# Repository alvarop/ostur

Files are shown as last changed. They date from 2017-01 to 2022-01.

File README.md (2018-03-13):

# Ostur - Cheese cave controller!

This is a work in progress for a cheese cave controller system.
The goal is to be able to control a mini fridge to get the right conditions for cheesemaking.

The project consists of:

* [Hardware](hw/) - A microcontroller and various temperature/humidity sensors
* [Firmware](fw/2.0/) - Code in the microcontroller to control the fridge and measure temperature/humidity values
* [Software](sw/2.0/) - Python scripts to communicate with the microcontroller to log and plot data

So far, it's been used to [make Brie](https://imgur.com/a/cGHID) [successfully](https://imgur.com/B5qB1kU)!

Once it's more user friendly, I'll add usage instructions so others can reproduce the setup.

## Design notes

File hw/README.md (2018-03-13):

# Ostur Hardware

To make some brie, there are 3 main components required:
1. An [Ostur controller](controller/) PCB
2. A controllable power outlet relay module. I'm using [this one](https://www.adafruit.com/product/2935) from Adafruit
3. 2+ [Ostur temperature/humidity sensors](humidity/). One for the fridge temperature and the rest for each aging container (if any).

Optional components are:
1. [Silicon Labs BLED112](https://www.digikey.com/products/en?keywords=1446-1030-ND) USB dongle for receiving BLE beacon data of the temperature/humidity.

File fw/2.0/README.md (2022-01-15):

# Ostur Firmware

The latest Ostur hardware uses the NRF52 microcontroller and the [Apache Mynewt](https://mynewt.apache.org/) OS for the firmware.

## Building the Firmware

1. Install the newt tool. [Instructions here](https://mynewt.apache.org/os/get_started/get_started/).
2. Install the [GNU Arm Embedded Toolchain](https://developer.arm.com/open-source/gnu-toolchain/gnu-rm/downloads)
3. Clone this repo `git clone https://github.com/alvarop/ostur.git`
4. Cd into the fw directory (this one) `cd fw/2.0/`
5. Run `newt install` to get the Mynewt libraries
6. Run `newt build ostur_sensor_boot` to build the bootloader
7. Run `newt build ostur_sensor`

## Loading the Firmware (using an [NRF52DK](https://www.nordicsemi.com/eng/Products/Bluetooth-low-energy/nRF52-DK) as a programmer)
1. Make sure the [JLink tools](https://www.segger.com/downloads/jlink/) are installed
2. Connect the **Debug Out** connector on the NRF52DK (or on any JLink programmer) to the Ostur's SWD connector (on the bottom)
3. Run `newt load ostur_sensor_boot` to load the bootloader
4. Run `newt run ostur_sensor 0` to load the main firmware and enter a gdb debugging session. Press `c + enter` to start running the code.

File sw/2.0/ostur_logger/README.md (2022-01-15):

# Ostur Logger Setup

## On Raspberry Pi

1. Clone repo to raspberry pi (or scp it over)
2. Run `./support/install_dependencies.sh` to get required software
3. Run `./support/setup.sh` to configure everything and start the server

If you just changed a few files and don't want to go through the whole pipenv process again, you can use `./support/update.sh`. This will just restart the services.

### Monitoring
To monitor packets arriving run:

`sudo tail -f /var/log/supervisor/ostur-logger-app-stdout---supervisor-KsDl4b.log`

Note that the last few characters, `KsDl4b` in this case, change everytime supervisor restarts. It's easy to just tab complete with whatever is there.

To check for errors, just replace stdout for stderr in the command.

## Local Development
`pip install -r requirements.txt`
Run `pipenv run python ostur_logger.py --port /dev/ttyUSB0 --baud_rate 115200 --db sqlite_db_filename.db`

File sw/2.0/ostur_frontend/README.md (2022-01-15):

# Ostur Frontend Setiup

## On Raspberry Pi

1. Clone repo to raspberry pi (or scp it over)
2. Run `./support/install_dependencies.sh` to get required software
3. Run `./support/setup.sh` to configure everything and start the server

**NOTE:** Python files copied over to /var/flaskapp/ostur_frontend, so if you edit the ones here, it won't change.

If you just changed a few files and don't want to go through the whole pipenv process again, you can use `./support/update.sh`. This will just rsync the changed files over and restart the services.

## Local Development

### Gunicorn
`pip install -r requirements.txt`
Run `export DATABASE=/path/to/ostur.db; pipenv run gunicorn --reload src:app`

### Flask Profiler

Temporarily install `pipenv install werkzeug`

Run `export DATABASE=/path/to/ostur.db; pipenv run python ./src/profile-flask.py`

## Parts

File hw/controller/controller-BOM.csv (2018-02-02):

Title | Ostur Controller
Revision | 2.0
Date | 2018-01-22
Generated | Fri 02 Feb 2018 03:28:43 AM PST
Company | alvarop.com
Comment 1
Comment 2
Comment 3
Comment 4
Total Parts | 49
Total Unique Parts | 29
Ref | Qty | Value | Footprint | MPN
AE1 | 1 | Antenna | alvarop:AMCA31-2R450G-S1F-T3
C10 C11 C5 | 3 | 1uF | Capacitors_SMD:C_0603 | CL21F105ZAFNNNG
C2 | 1 | 10nF | Capacitors_SMD:C_0603 | CL21B103KBANNNC
C17 C4 C6 C1 | 4 | 100nF | Capacitors_SMD:C_0603 | CL21B104MBCNNNC
C9 C3 | 2 | 4.7uF | Capacitors_SMD:C_0603 | CL21A475KQFNNNG
C12 C7 | 2 | 12pF | Capacitors_SMD:C_0603
C8 | 1 | 100pF | Capacitors_SMD:C_0603
C13 | 1 | 0.8pF | Capacitors_SMD:C_0603
C14 C15 | 2 | DNP | Capacitors_SMD:C_0603
D3 | 1 | LED2 | LEDs:LED_0603 | LG R971-KN-1
D2 | 1 | LED1 | LEDs:LED_0603 | LG R971-KN-1
D1 | 1 | LED0 | LEDs:LED_0603 | LG R971-KN-1
J2 | 1 | USB_OTG | footprints:USB_MICRO_B | 10118192-0001LF
J3 | 1 | UART | Pin_Headers:Pin_Header_Straight_1x03_Pitch1.27mm
J1 | 1 | ARM-SWD | alvarop:ARM_SWD_SMD
L1 | 1 | 3.9nH | Resistors_SMD:R_0603
P14 | 1 | I2C0 | Pin_Headers:Pin_Header_Straight_1x04_Pitch2.54mm
P15 | 1 | I2C1 | Pin_Headers:Pin_Header_Straight_1x04_Pitch2.54mm
P16 | 1 | I2C2 | Pin_Headers:Pin_Header_Straight_1x04_Pitch2.54mm
P17 | 1 | I2C3 | Pin_Headers:Pin_Header_Straight_1x04_Pitch2.54mm
P2 | 1 | FRIDGE | Pin_Headers:Pin_Header_Straight_1x02_Pitch2.54mm
R5 R4 R3 | 3 | 680 | Resistors_SMD:R_0603 | RC0805JR-07680RL
R11 R12 R9 R10 R13 R14 R21 R22 R23 R24 R26 | 11 | 10k | Resistors_SMD:R_0603 | 311-10KARCT-ND
R1 | 1 | 0 | Resistors_SMD:R_0603
U3 | 1 | tca9546a | Housings_SSOP:TSSOP-16_4.4x5mm_Pitch0.65mm | TCA9546APWR
U2 | 1 | MIC550X | footprints:SOT-23(M5)
U8 | 1 | SHT3x-DIS | footprints:SHT3x
U1 | 1 | NRF52810-QCAA | alvarop:NRF52810_QCAA_QFN32
Y1 | 1 | 32MHz | Crystals:Crystal_SMD_2016-4pin_2.0x1.6mm | CX2016DB32000D0FLJCC
BOM made with KICAD_BOM_WIZARD (https://github.com/HashDefineElectronics/KiCad_BOM_Wizard.git)
Generated Fri 02 Feb 2018 03:28:43 AM PST

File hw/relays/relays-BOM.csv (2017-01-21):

Title
Revision
Date
Generated | Fri 20 Jan 2017 06:25:38 PM PST
Company
Comment 1
Comment 2
Comment 3
Comment 4
Total Parts | 8
Total Unique Parts | 6
Ref | Qty | Value | Footprint | MPN
D1 | 1 | D | footprints:SOD-80 | LL4148
K1 | 1 | EE2-3NU | footprints:EE2-3NU | EE2-3NU-L
P1 | 1 | CONN_01X03 | Pin_Headers:Pin_Header_Straight_1x03
P2 P3 P4 | 3 | CONN_01X02 | Pin_Headers:Pin_Header_Straight_1x02
Q1 | 1 | MMBT3904 | TO_SOT_Packages_SMD:SOT-23 | MMBT3904 215
R1 | 1 | 1k1 | Resistors_SMD:R_0805 | RMCF0805JT1K00
BOM made with KICAD_BOM_WIZARD (https://github.com/HashDefineElectronics/KiCad_BOM_Wizard.git)
Generated Fri 20 Jan 2017 06:25:38 PM PST

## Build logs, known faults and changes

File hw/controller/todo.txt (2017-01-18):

Add jumper for 5V/3V from UART1 connector
Add silkscreen to mark uart3/spi ground and power

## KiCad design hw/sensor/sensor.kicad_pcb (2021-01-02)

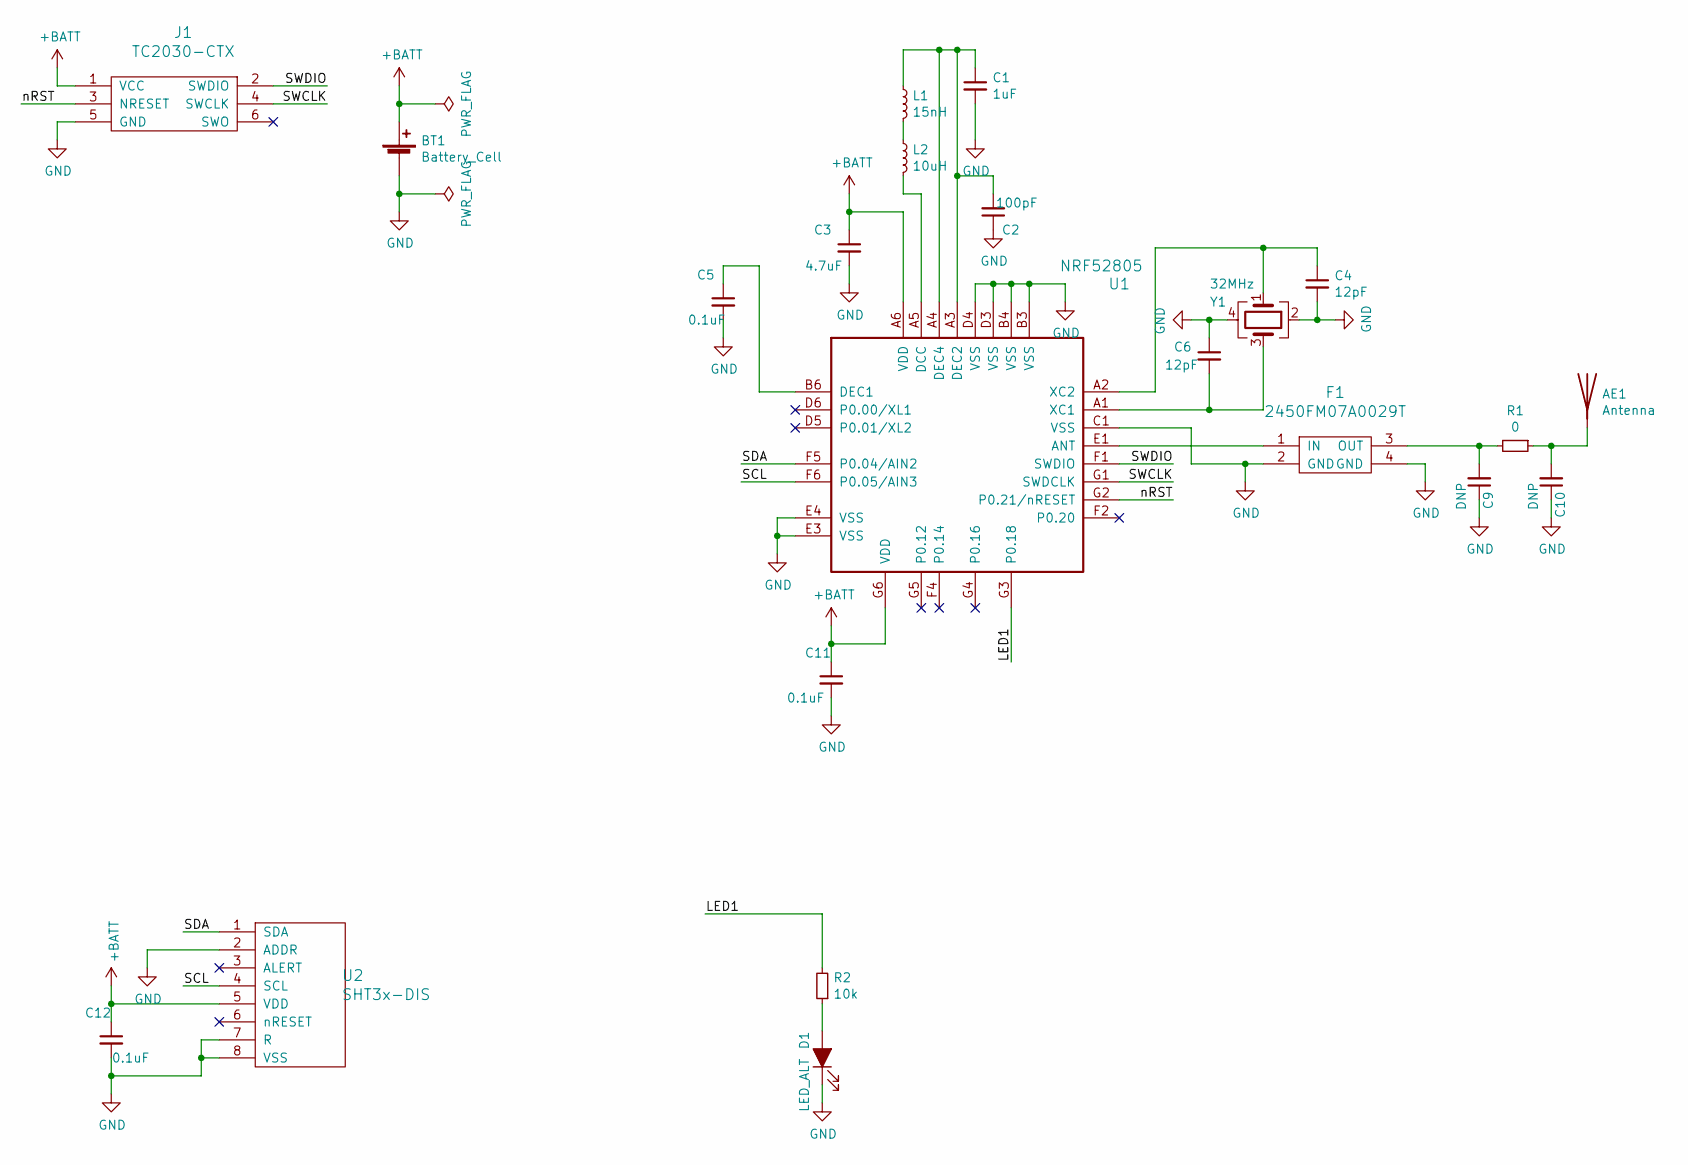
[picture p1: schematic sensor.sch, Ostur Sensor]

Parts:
AE1: Antenna; AMCA31-2R450G-S1F-T3; MPN AMCA31-2R450G-S1F-T3
BT1: Battery_Cell; BAT-HLD-001-THM; MPN BATT-HLD-001-THM
C1: 1uF; C_0402_1005Metric; MPN CC0402KRX5R5BB105
C2: 100pF; C_0402_1005Metric; MPN UMK105CG101JV-F
C3: 4.7uF; C_0402_1005Metric; MPN GRM155R60J475ME47D
C4, C6: 12pF; C_0402_1005Metric; MPN C0402C120J5GACTU
C5, C11, C12: 0.1uF; C_0402_1005Metric; MPN GRM155R61A104KA01D
C9, C10: DNP; C_0402_1005Metric
D1: LED_ALT; LED_0402_1005Metric; MPN QBLP595-IG
F1: 2450FM07A0029T; MPN 2450FM07A0029T
J1: TC2030-CTX; TC2030-NL
L1: 15nH; L_0402_1005Metric; MPN HK100515NJ-T‎
L2: 10uH; L_0603_1608Metric; MPN ‎LQM18FN100M00D‎
R1: 0; R_0402_1005Metric; MPN RC1005J000CS
R2: 10k; R_0402_1005Metric; MPN RC0402JR-0710KL
U1: NRF52805; MPN NRF52805-CAAA-R
U2: SHT3x-DIS; SHT3x; MPN SHT30-DIS-P2.5KS
Y1: 32MHz; Crystal_SMD_2016-4Pin_2.0x1.6mm; MPN CX2016DB32000D0FLJCC

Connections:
+BATT: BT1.1 (+), C3.1, C11.1, C12.1, J1.1 (VCC), U1.A6 (VDD), U1.G6 (VDD), U2.5 (VDD)
/LED1: R2.2, U1.G3 (P0.18)
/SCL: U1.F6 (P0.05/AIN3), U2.4 (SCL)
/SDA: U1.F5 (P0.04/AIN2), U2.1 (SDA)
/SWCLK: J1.4 (SWCLK), U1.G1 (SWDCLK)
/SWDIO: J1.2 (SWDIO), U1.F1 (SWDIO)
/nRST: J1.3 (NRESET), U1.G2 (P0.21/nRESET)
GND: BT1.2 (-), C1.2, C2.1, C3.2, C4.2, C5.2, C6.1, C9.1, C10.1, C11.2, C12.2, D1.1 (K), F1.2 (GND), F1.4 (GND), J1.5 (GND), U1.B3 (VSS), U1.B4 (VSS), U1.C1 (VSS), U1.D3 (VSS), U1.D4 (VSS), U1.E3 (VSS), U1.E4 (VSS), U2.2 (ADDR), U2.7 (R), U2.8 (VSS), Y1.2, Y1.4
unnamed: AE1.1, C10.2, R1.1
unnamed: C1.1, C2.2, L1.1, U1.A3 (DEC2), U1.A4 (DEC4)
unnamed: C4.1, U1.A2 (XC2), Y1.1
unnamed: C5.1, U1.B6 (DEC1)
unnamed: C6.2, U1.A1 (XC1), Y1.3
unnamed: C9.2, F1.3 (OUT), R1.2
unnamed: D1.2 (A), R2.1
unnamed: F1.1 (IN), U1.E1 (ANT)
unnamed: L1.2, L2.1
unnamed: L2.2, U1.A5 (DCC)

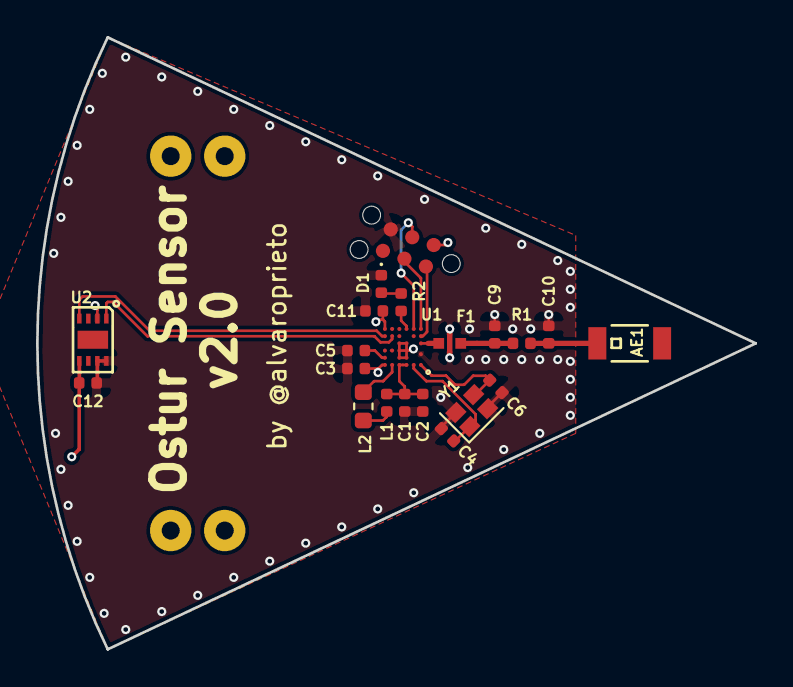
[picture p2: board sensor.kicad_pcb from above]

Board: 4 copper layers, 39.9 x 34.0 mm, 22 parts (1 on the bottom side), 18 nets.

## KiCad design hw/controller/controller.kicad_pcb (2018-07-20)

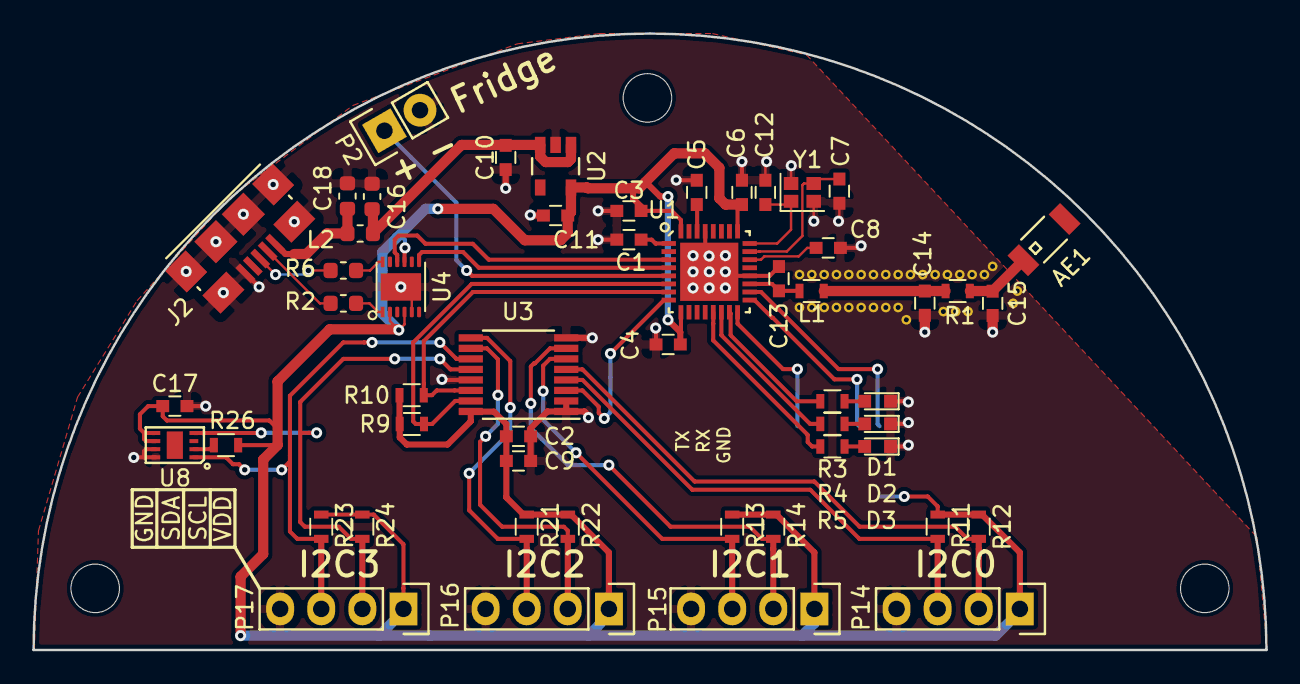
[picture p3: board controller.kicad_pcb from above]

Board: 2 copper layers, 76.2 x 38.1 mm, 54 parts (1 on the bottom side), 40 nets.

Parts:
AE1: Antenna; AMCA31-2R450G-S1F-T3
C1, C4, C6, C17: 100nF; C_0603
C2: 10nF; C_0603
C3, C9: 4.7uF; C_0603
C5, C10, C11: 1uF; C_0603
C7, C12: 12pF; C_0603
C8: 100pF; C_0603
C13: 0.8pF; C_0603
C14, C15: DNP; C_0603
C16: 100nF; C_0603_1608Metric
C18: 10nF; C_0603_1608Metric
D1: LED0; LED_0603
D2: LED1; LED_0603
D3: LED2; LED_0603
J1: ARM-SWD; ARM_SWD_SMD
J2: USB_OTG; USB_MICRO_B
L1: 3.9nH; R_0603
L2: FB; R_0603_1608Metric
P2: FRIDGE; Pin_Header_Straight_1x02
P14: I2C0; Pin_Header_Straight_1x04
P15: I2C1; Pin_Header_Straight_1x04
P16: I2C2; Pin_Header_Straight_1x04
P17: I2C3; Pin_Header_Straight_1x04
R1: 0; R_0603
R2, R6: 27; R_0603_1608Metric
R3, R4, R5: 680; R_0603
R9, R10, R11, R12, R13, R14, R21, R22, R23, R24, R26: 10k; R_0603
U1: NRF52810-QCAA; NRF52810_QCAA_QFN32
U2: MIC550X; SOT-23(M5)
U3: tca9546a; TSSOP-16_4.4x5mm_Pitch0.65mm
U4: FT234XD; FTDI_DFN12
U8: SHT3x-DIS; SHT3x
Y1: 32MHz; Crystal_SMD_2016-4pin_2.0x1.6mm

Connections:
+5V: C10.1, C16.1, L2.2, U2.1, U2.3
/ADDR_LOCAL: R26.1, U8.2
/FRIDGE: P2.1, U1.5
/LED0: R3.2, U1.15
/LED1: R4.2, U1.14
/LED2: R5.2, U1.13
/SCL: R10.2, U1.7, U3.14
/SCL0: P14.2, R12.2, U3.5
/SCL1: P15.2, R14.2, U3.7
/SCL2: P16.2, R22.2, U3.10
/SCL3: P17.2, R24.2, U3.12, U8.4
/SDA: R9.2, U1.6, U3.15
/SDA0: P14.3, R11.2, U3.4
/SDA1: P15.3, R13.2, U3.6
/SDA2: P16.3, R21.2, U3.9
/SDA3: P17.3, R23.2, U3.11, U8.1
/SWDCLK: J1.4, U1.17
/SWDIO: J1.2, U1.18
/TCA_nRST: U1.8, U3.3
/UART1_RX: U1.4, U4.7
/UART1_TX: U1.3, U4.10
/USB_DM: J2.2, R2.1
/USB_DP: J2.3, R6.2
/VDD_5: C18.1, J2.1, L2.1
/nRST: J1.10, U1.16
GND: C1.2, C2.2, C3.2, C4.2, C5.2, C6.2, C7.2, C8.1, C9.2, C10.2, C11.2, C12.1, C13.1, C14.1, C15.1, C16.2, C17.2, C18.2, D1.1, D2.1, D3.1, J1.3, J1.5, J2.5, J2.6, P2.2, P14.4, P15.4, P16.4, P17.4, U1.20, U1.29, U2.2, U3.1, U3.2, U3.8, U3.13, U4.5, U8.7, U8.8, Y1.2, Y1.4
unnamed: AE1.1, C15.2, R1.2
unnamed: C1.1, U1.1
unnamed: C5.1, U1.30
unnamed: C7.1, U1.23, Y1.3
unnamed: C8.2, U1.22
unnamed: C12.2, U1.24, Y1.1
unnamed: C13.2, L1.1, U1.19
unnamed: C14.2, L1.2, R1.1
unnamed: D1.2, R3.1
unnamed: D2.2, R4.1
unnamed: D3.2, R5.1
unnamed: R2.2, U4.1
unnamed: R6.1, U4.12
VDD: C2.1, C3.1, C4.1, C6.1, C9.1, C11.1, C17.1, J1.1, P14.1, P15.1, P16.1, P17.1, R9.1, R10.1, R11.1, R12.1, R13.1, R14.1, R21.1, R22.1, R23.1, R24.1, R26.2, U1.9, U1.25, U1.32, U2.5, U3.16, U4.2, U4.4, U4.9, U8.5, U8.6

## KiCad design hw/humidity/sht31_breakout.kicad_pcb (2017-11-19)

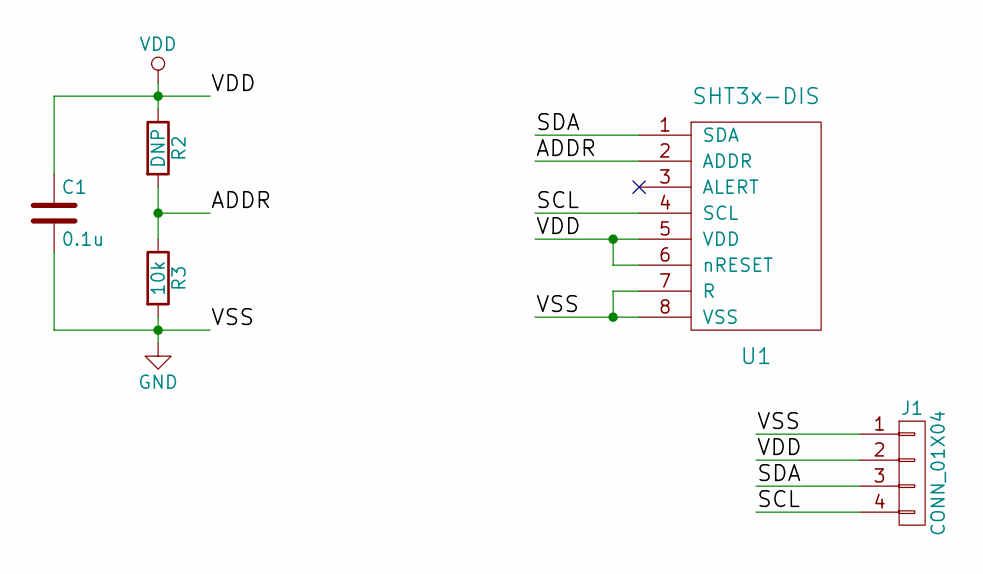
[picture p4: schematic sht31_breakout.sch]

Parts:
C1: 0.1u; C_0603
J1: CONN_01X04; Pin_Header_Straight_1x04_Pitch2.54mm
R2: DNP; C_0603
R3: 10k; C_0603
U1: SHT3x-DIS; SHT3x

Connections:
/ADDR: R2.2, R3.1, U1.2 (ADDR)
/SCL: J1.4, U1.4 (SCL)
/SDA: J1.3, U1.1 (SDA)
GND: C1.2, J1.1, R3.2, U1.7 (R), U1.8 (VSS)
VDD: C1.1, J1.2, R2.1, U1.5 (VDD), U1.6 (nRESET)

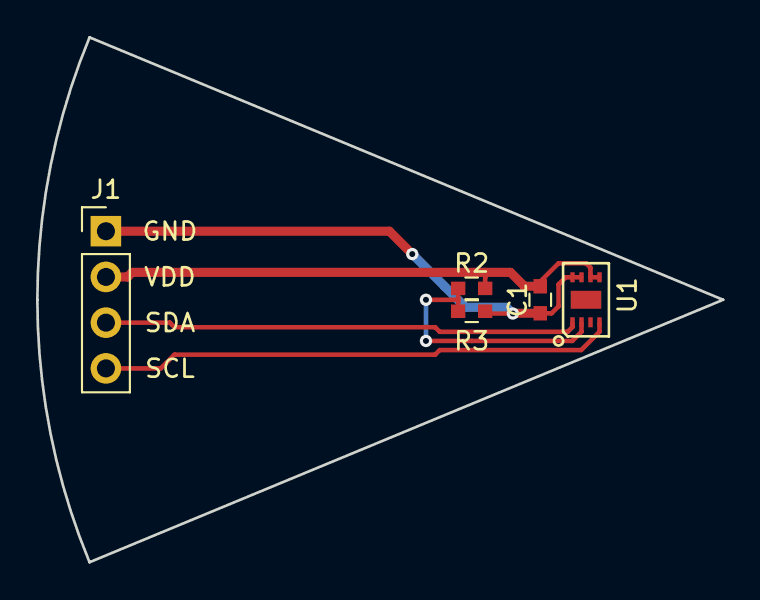
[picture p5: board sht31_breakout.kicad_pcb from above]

Board: 2 copper layers, 38.1 x 29.2 mm, 5 parts (0 on the bottom side), 5 nets.

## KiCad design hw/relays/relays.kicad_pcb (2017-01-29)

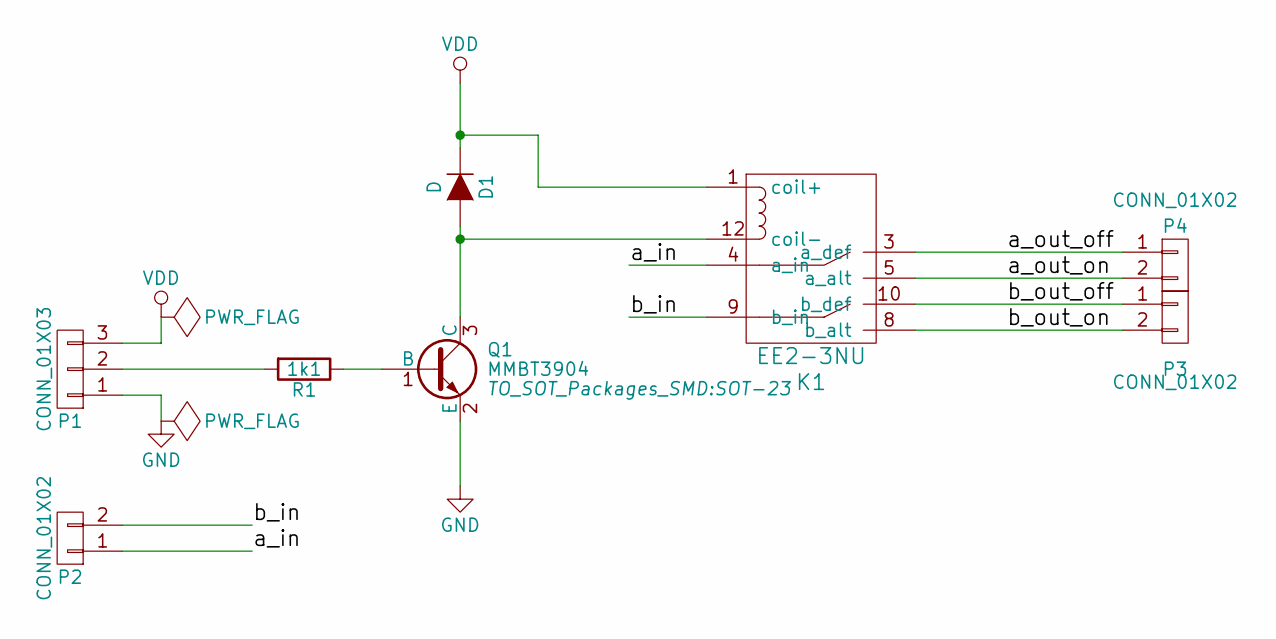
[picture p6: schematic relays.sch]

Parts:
D1: D; SOD-80; MPN LL4148
K1: EE2-3NU; MPN EE2-3NU-L
P1: CONN_01X03; Pin_Header_Straight_1x03
P2, P3, P4: CONN_01X02; Pin_Header_Straight_1x02
Q1: MMBT3904; SOT-23; MPN MMBT3904,215
R1: 1k1; R_0805; MPN RMCF0805JT1K00

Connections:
/a_in: K1.4 (a_in), P2.1
/a_out_off: K1.3 (a_def), P4.1
/a_out_on: K1.5 (a_alt), P4.2
/b_in: K1.9 (b_in), P2.2
/b_out_off: K1.10 (b_def), P3.1
/b_out_on: K1.8 (b_alt), P3.2
GND: P1.1, Q1.2 (E)
unnamed: D1.2 (A), K1.12 (coil-), Q1.3 (C)
unnamed: P1.2, R1.2
unnamed: Q1.1 (B), R1.1
VDD: D1.1 (K), K1.1 (coil+), P1.3

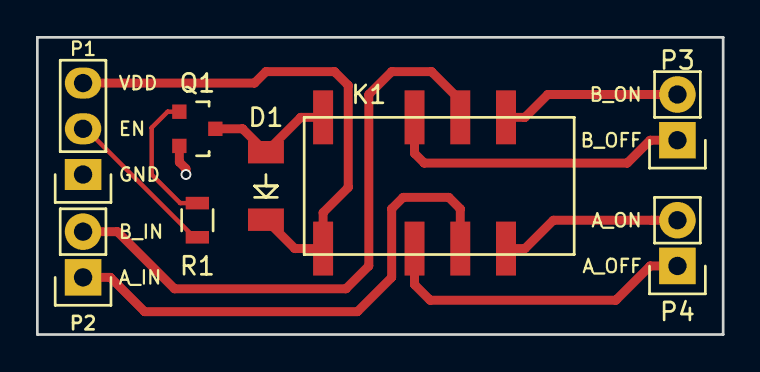
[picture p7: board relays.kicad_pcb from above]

Board: 2 copper layers, 38.1 x 16.5 mm, 8 parts (0 on the bottom side), 11 nets.

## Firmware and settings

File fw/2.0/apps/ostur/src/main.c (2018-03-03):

#include <assert.h>
#include <string.h>

#include "sysinit/sysinit.h"
#include "os/os.h"
#include "console/console.h"
#include "bsp/bsp.h"
#include "hal/hal_gpio.h"
#include "i2c/i2c.h"
#include "tca95xxa/tca95xxa.h"
#include "sht3x/sht3x.h"

#if MYNEWT_VAL(USE_BLE)
#include <host/ble_hs.h>
#endif

#define OSTUR_TASK_PRI         (20)
#define OSTUR_STACK_SIZE       (256)
struct os_task ostur_task;
os_stack_t ostur_task_stack[OSTUR_STACK_SIZE];

#define FRIDGE_TASK_PRI         (10)
#define FRIDGE_STACK_SIZE       (64)
struct os_task fridge_task;
os_stack_t fridge_task_stack[FRIDGE_STACK_SIZE];

#define BLINK_TASK_PRI         (99)
#define BLINK_STACK_SIZE       (64)
struct os_task blink_task;
os_stack_t blink_task_stack[BLINK_STACK_SIZE];

static volatile uint16_t timestamp;

static volatile bool fridge_on;
static bool fridge_running = false;

#define NUM_SAMPLES 8

static int16_t primary_buff[NUM_SAMPLES];
static int16_t outside_buff[NUM_SAMPLES];
static uint16_t buff_index;

static const int16_t temp_setting = (int16_t)(MYNEWT_VAL(TEMP_SETTING_C) * 100);

#define MAX_SENSORS 8
#define PRIMARY_SENSOR 0
#define OUTSIDE_SENSOR (7)

typedef struct {
  uint8_t bus;
  uint8_t addr;
  bool enabled;
  int16_t temperature;
  int16_t humidity;
} th_sensor_t;

th_sensor_t sensors[MAX_SENSORS] = {
    {0, SHT3x_ADDR,     false},
    {0, SHT3x_ALT_ADDR, false},
    {1, SHT3x_ADDR,     false},
    {1, SHT3x_ALT_ADDR, false},
    {2, SHT3x_ADDR,     false},
    {2, SHT3x_ALT_ADDR, false},
    {3, SHT3x_ADDR,     false},
    {3, SHT3x_ALT_ADDR, false},
};

#if MYNEWT_VAL(USE_BLE)
#define BEACON_MAGIC 0x0578

typedef struct {
    uint16_t magic;
    uint32_t device_id;
    uint16_t timestamp;
    uint8_t sensor_ch;
    uint8_t fridge_state;
    int16_t temperature;
    int16_t humidity;
    uint16_t flags;
} __attribute__((packed)) ble_beacon_t;

static ble_beacon_t beacon_data;

static void ble_app_advertise(bool);

static uint8_t adv_sensor_ch;

static int gap_event_cb(struct ble_gap_event *event, void *arg) {
    switch (event->type) {

    case BLE_GAP_EVENT_ADV_COMPLETE:
        ble_app_advertise(false);
        break;
    }
    return 0;
}

static void ble_app_set_addr(void) {
    ble_addr_t addr;
    int rc;

    rc = ble_hs_id_gen_rnd(1, &addr);
    assert(rc == 0);

    rc = ble_hs_id_set_rnd(addr.val);
    assert(rc == 0);
}

// Use a BLE_CH_ADV_TIME_MS long beacon to send each individual
// channel's data
static void ble_app_advertise(bool first_tx) {
    struct ble_gap_adv_params adv_params;
    struct ble_hs_adv_fields fields;
    int rc;

    if(first_tx) {
        adv_sensor_ch = 0;
        beacon_data.device_id = NRF_FICR->DEVICEADDR[0];
        beacon_data.timestamp = timestamp;
        beacon_data.fridge_state = fridge_running;
        beacon_data.flags = 0;
    }

    // Find the next enabled sensor
    while(adv_sensor_ch < MAX_SENSORS && !sensors[adv_sensor_ch].enabled) {
        adv_sensor_ch++;
    }

    if(adv_sensor_ch < MAX_SENSORS) {
        beacon_data.sensor_ch = adv_sensor_ch;
        beacon_data.temperature = sensors[adv_sensor_ch].temperature;
        beacon_data.humidity = sensors[adv_sensor_ch].humidity;

        fields = (struct ble_hs_adv_fields){ 0 };
        rc = ble_eddystone_set_adv_data_uid(&fields, &beacon_data);
        assert(rc == 0);

        adv_params = (struct ble_gap_adv_params){ 0 };
        rc = ble_gap_adv_start(
            BLE_OWN_ADDR_RANDOM,
            NULL,
            MYNEWT_VAL(BLE_CH_ADV_TIME_MS),
            &adv_params,
            gap_event_cb,
            NULL);
        assert(rc == 0);

        adv_sensor_ch++;
    }
}

static void ble_app_on_sync(void) {
    /* Generate a non-resolvable private address. */
    ble_app_set_addr();
}
#endif

void fridge_control(bool enable) {
    if(enable) {
        hal_gpio_write(FRIDGE_PIN, 1);
        hal_gpio_write(LED_2_PIN, 1);
        console_printf("Enabling fridge\n");
    } else {
        hal_gpio_write(FRIDGE_PIN, 0);
        hal_gpio_write(LED_2_PIN, 0);
        console_printf("Disabling fridge\n");
    }
}

void fridge_task_fn(void *arg) {

    hal_gpio_init_out(FRIDGE_PIN, 0);
    hal_gpio_init_out(LED_2_PIN, 0);

    while(1) {
        if(!fridge_running && fridge_on) {
            fridge_running = true;
            fridge_control(true);
        } else if(fridge_running && !fridge_on) {
            fridge_running = false;
            fridge_control(false);
            os_time_delay(MYNEWT_VAL(FRIDGE_OFF_TIME_M) * OS_TICKS_PER_SEC * 60);
        }

        os_time_delay(OS_TICKS_PER_SEC);
    }
}

void ostur_task_fn(void *arg) {
    int32_t outside_avg;
    int32_t primary_avg;

    hal_gpio_init_out(LED_1_PIN, 0);
    hal_gpio_init_out(TCA_NRST_PIN, 1);

    console_printf("Ostur Controller v2.0\n");

    i2c_init(0, SDA_PIN, SCL_PIN, 100);

    #if MYNEWT_VAL(USE_BLE)
        beacon_data.magic = BEACON_MAGIC;
        beacon_data.timestamp = 0;
    #endif

    console_printf("Detecting HT Sensors\n");
    int32_t rval;
    for(uint8_t sensor=0; sensor < MAX_SENSORS; sensor++) {
        tca95xxa_set_channel(0x70, sensors[sensor].bus);
        rval = sht3x_init(sensors[sensor].addr);
        console_printf("%d:0x%02X - %ld\n", sensors[sensor].bus, SHT3x_ADDR, rval);
        if (rval == 0) {
            sensors[sensor].enabled = true;
        }
    }

    if(sensors[OUTSIDE_SENSOR].enabled == false) {
        console_printf("Error! Outside sensor not present\n");
    }

    if(sensors[PRIMARY_SENSOR].enabled == false) {
        console_printf("Error! Primary sensor not present\n");
    }

    // TODO: Blink differently or advertise error here

    // Take a bunch of samples to initialize the buffer
    for(uint16_t sample = 0; sample < NUM_SAMPLES; sample++) {
        int16_t temp;
        tca95xxa_set_channel(0x70, sensors[OUTSIDE_SENSOR].bus);
        rval = sht3x_read(sensors[OUTSIDE_SENSOR].addr, &temp, NULL);
        outside_buff[sample] = temp;

        tca95xxa_set_channel(0x70, sensors[PRIMARY_SENSOR].bus);
        rval = sht3x_read(sensors[PRIMARY_SENSOR].addr, &temp, NULL);
        primary_buff[sample] = temp;
    }

    while (1) {
        os_time_delay(OS_TICKS_PER_SEC * MYNEWT_VAL(SAMPLE_RATE_S));

        hal_gpio_init_out(LED_1_PIN, 1);
        for(uint8_t sensor=0; sensor < MAX_SENSORS; sensor++) {
            if (!sensors[sensor].enabled) {
                continue;
            }
            int16_t *temp = &sensors[sensor].temperature;
            int16_t *humidity = &sensors[sensor].humidity;

            tca95xxa_set_channel(0x70, sensors[sensor].bus);
            rval = sht3x_read(sensors[sensor].addr, temp, humidity);
            console_printf("s: %d t:%d h:%d\n", sensor, *temp, *humidity);
        }

        // Update primary/outside buffers for average
        outside_buff[buff_index] = sensors[OUTSIDE_SENSOR].temperature;
        primary_buff[buff_index] = sensors[PRIMARY_SENSOR].temperature;
        buff_index =  (buff_index + 1) & (NUM_SAMPLES - 1);

        outside_avg = 0;
        primary_avg = 0;

        // Compute averages
        for(uint16_t index = 0; index < NUM_SAMPLES; index++){
            outside_avg += outside_buff[index];
            primary_avg += primary_buff[index];
        }

        outside_avg /= NUM_SAMPLES;
        primary_avg /= NUM_SAMPLES;

        if ((primary_avg > temp_setting) && (temp_setting < outside_avg)) {
            fridge_on = true;
        } else {
            fridge_on = false;
        }

#if MYNEWT_VAL(USE_BLE)

        ble_app_advertise(true);
#endif

        hal_gpio_init_out(LED_1_PIN, 0);

        timestamp++;
    }
}

void blink_task_fn(void *arg) {

    hal_gpio_init_out(LED_0_PIN, 0);

    while(1) {
        os_time_delay(OS_TICKS_PER_SEC);
        hal_gpio_toggle(LED_0_PIN);
    }

}

int
main(int argc, char **argv)
{
    sysinit();

    os_task_init(
        &blink_task,
        "blink_task",
        blink_task_fn,
        NULL,
        BLINK_TASK_PRI,
        OS_WAIT_FOREVER,
        blink_task_stack,
        BLINK_STACK_SIZE);

    os_task_init(
        &fridge_task,
        "fridge_task",
        fridge_task_fn,
        NULL,
        FRIDGE_TASK_PRI,
        OS_WAIT_FOREVER,
        fridge_task_stack,
        FRIDGE_STACK_SIZE);

    os_task_init(
        &ostur_task,
        "ostur_task",
        ostur_task_fn,
        NULL,
        OSTUR_TASK_PRI,
        OS_WAIT_FOREVER,
        ostur_task_stack,
        OSTUR_STACK_SIZE);

#if MYNEWT_VAL(USE_BLE)
     ble_hs_cfg.sync_cb = ble_app_on_sync;
#endif

    while(1) {
        os_eventq_run(os_eventq_dflt_get());
    }

    assert(0);

    return 0;
}

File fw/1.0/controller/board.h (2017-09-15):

#ifndef __BOARD_H__
#define __BOARD_H__

#include "stm32f0xx.h"

#define LED0_PORT GPIOB
#define LED0_PIN 0

#define LED1_PORT GPIOB
#define LED1_PIN 1

#define LED2_PORT GPIOB
#define LED2_PIN 2

#define UART1_TX_PORT GPIOA
#define UART1_TX_PIN 9

#define UART1_RX_PORT GPIOA
#define UART1_RX_PIN 10

#define SDA_PORT GPIOB
#define SDA_PIN 7

#define SCL_PORT GPIOB
#define SCL_PIN 6

#define TCA_nRST_PORT GPIOB
#define TCA_nRST_PIN 8

#define MIST_PORT GPIOA
#define MIST_PIN 3

#define PUMP_PORT GPIOA
#define PUMP_PIN 4

#define FAN_PORT GPIOA
#define FAN_PIN 5

#define FRIDGE_PORT GPIOA
#define FRIDGE_PIN 6

#endif  // __BOARD__

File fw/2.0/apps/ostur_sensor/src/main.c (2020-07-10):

#include <assert.h>
#include <string.h>

#include <sysinit/sysinit.h>
#include <os/os.h>
#include <console/console.h>
#include <bsp/bsp.h>
#include <hal/hal_gpio.h>
#include <i2c/i2c.h>
#include <sht3x/sht3x.h>
#include <simple_adc/simple_adc.h>

#if MYNEWT_VAL(USE_BLE)
#include <host/ble_hs.h>
#endif

// Magic value that identifies ble beacon as ostur packet
#define OSTUR_MAGIC (0x5757)

#define OSTUR_TASK_PRI         (20)
#define OSTUR_STACK_SIZE       (256)
struct os_task ostur_task;
os_stack_t ostur_task_stack[OSTUR_STACK_SIZE];

static volatile uint16_t timestamp;

#if MYNEWT_VAL(USE_BLE)

typedef struct {
    uint32_t device_id;
    uint16_t timestamp;
    int16_t temperature;
    int16_t humidity;
    uint16_t batt;
    uint16_t flags;
    uint16_t magic;
} __attribute__((packed)) ble_beacon_t;

static ble_beacon_t beacon_data;

static void ble_app_advertise();

static int gap_event_cb(struct ble_gap_event *event, void *arg) {
    switch (event->type) {

    case BLE_GAP_EVENT_ADV_COMPLETE:
        // ble_app_advertise();
        break;
    }
    return 0;
}

static void ble_app_set_addr(void) {
    ble_addr_t addr;
    int rc;

    rc = ble_hs_id_gen_rnd(1, &addr);
    assert(rc == 0);

    rc = ble_hs_id_set_rnd(addr.val);
    assert(rc == 0);
}

// Use a BLE_CH_ADV_TIME_MS long beacon to send each individual
// channel's data
static void ble_app_advertise() {
    struct ble_gap_adv_params adv_params;
    struct ble_hs_adv_fields fields;
    int rc;

    beacon_data.device_id = NRF_FICR->DEVICEADDR[0];
    beacon_data.timestamp = timestamp;
    beacon_data.flags = 0;
    beacon_data.magic = OSTUR_MAGIC;

    fields = (struct ble_hs_adv_fields){ 0 };
    
    rc = ble_eddystone_set_adv_data_uid(&fields, &beacon_data, 0);
    assert(rc == 0);

    adv_params = (struct ble_gap_adv_params){ 0 };
    rc = ble_gap_adv_start(
        BLE_OWN_ADDR_RANDOM,
        NULL,
        MYNEWT_VAL(BLE_CH_ADV_TIME_MS),
        &adv_params,
        gap_event_cb,
        NULL);
    assert(rc == 0);

}

static void ble_app_on_sync(void) {
    /* Generate a non-resolvable private address. */
    ble_app_set_addr();
}
#endif

#define BATT_ADC_SAMPLES 16

void ostur_task_fn(void *arg) {

    console_printf("Ostur Sensor v1.0\n");

    #if MYNEWT_VAL(USE_BLE)
        beacon_data.timestamp = 0;
    #endif

    console_printf("Detecting HT Sensors\n");
    int32_t rval;

    rval = sht3x_init(SHT3x_ADDR);
    console_printf("0x%02X - %ld\n", SHT3x_ADDR, rval);
    if (rval != 0) {
        hal_gpio_write(LED2_PIN, 1);
        hal_gpio_write(LED1_PIN, 1);
        while(1){
            // TODO - Add retries/reboot after a while
            __asm("NOP;");
        }
    }

    // Wait a few seconds to start before sending first packet
    os_time_delay(OS_TICKS_PER_SEC * 5);

    while (1) {
        int32_t batt = 0;
        int32_t mv;

        hal_gpio_write(LED2_PIN, 1);

        // Sample battery and average over BATT_ADC_SAMPLES samples
        simple_adc_init();
        simple_adc_init_ch(0, NRF_SAADC_INPUT_VDD);
        for(uint8_t sample = 0; sample < BATT_ADC_SAMPLES; sample++){
            simple_adc_read_ch(0, &mv);
            batt += mv;
        }
        simple_adc_uninit();

#if MYNEWT_VAL(USE_BLE)
        beacon_data.batt = (uint16_t)(batt / BATT_ADC_SAMPLES);
#endif
        int16_t temperature, humidity;
        rval = sht3x_read(SHT3x_ADDR, &temperature, &humidity);

#if MYNEWT_VAL(USE_BLE)
        beacon_data.temperature = temperature;
        beacon_data.humidity = humidity;
#endif
        console_printf("t:%d h:%d\n", temperature, humidity);


#if MYNEWT_VAL(USE_BLE)

        ble_app_advertise();
#endif

        hal_gpio_write(LED2_PIN, 0);

        timestamp++;

        os_time_delay(OS_TICKS_PER_SEC * MYNEWT_VAL(SAMPLE_RATE_S));
    }
}


int
main(int argc, char **argv)
{
    sysinit();

    hal_gpio_init_out(LED1_PIN, 0);
    hal_gpio_init_out(LED2_PIN, 0);

    os_task_init(
        &ostur_task,
        "ostur_task",
        ostur_task_fn,
        NULL,
        OSTUR_TASK_PRI,
        OS_WAIT_FOREVER,
        ostur_task_stack,
        OSTUR_STACK_SIZE);

#if MYNEWT_VAL(USE_BLE)
     ble_hs_cfg.sync_cb = ble_app_on_sync;
#endif

    while(1) {
        os_eventq_run(os_eventq_dflt_get());
    }

    assert(0);

    return 0;
}

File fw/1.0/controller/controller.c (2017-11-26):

#include "controller.h"
#include <stdio.h>
#include <string.h>
#include "board.h"
#include "config.h"
#include "debug.h"
#include "i2c.h"
#include "rtc.h"
#include "sht31.h"
#include "stm32f0xx_conf.h"
#include "tca95xxa.h"
#include "timer.h"

typedef struct {
  int16_t temperature;
  int16_t humidity;
} __attribute__((packed)) th_value_t;

// NOTE: MUST be a power of 2
#define CONTROLLER_BUFF_SAMPLES (64)

// Time the fridge must be OFF before turning on again
#define FRIDGE_OFF_TIME_M (15)

static bool running = false;
static config_t *config;
static ms_timer_t controller_timer;
static ms_timer_t fridge_off_timer;
static th_value_t primary_buff[CONTROLLER_BUFF_SAMPLES];
static th_value_t outside_buff[CONTROLLER_BUFF_SAMPLES];
static uint16_t buff_index;

int32_t ControllerInit() {
  int32_t rval;
  config = ConfigGet();
  dprint(DEBUG, "%s\n", __func__);
  for (uint8_t sensor_id = 0; sensor_id < CONFIG_MAX_SENSORS; sensor_id++) {
    th_sensor_t *sensor = &config->sensor[sensor_id];
    if (sensor->addr != 0) {
      rval = Tca95xxaSetChannel(TCA95XXA_ADDR, sensor->bus);
      if (rval != 0) {
        dprint(ERR, "could not set i2c bus (%ld)\n", rval);
        GPIO_ResetBits(TCA_nRST_PORT, (1 << TCA_nRST_PIN));
        SleepMs(2);
        GPIO_SetBits(TCA_nRST_PORT, (1 << TCA_nRST_PIN));
        i2cSetup(100000);
        rval = Tca95xxaSetChannel(TCA95XXA_ADDR, sensor->bus);
        dprint(ERR, "Retry %d\n", rval);
        if (rval != 0) {
          break;
        }
        break;
      }

      Sht31Init(sensor->addr);
      if (rval != 0) {
        dprint(ERR, "SHT could not initialize (%ld)\n", rval);
        break;
      }
    }
  }

  for (uint16_t sample = 0; sample < CONTROLLER_BUFF_SAMPLES; sample++) {
    primary_buff[sample].temperature = 0;
    primary_buff[sample].humidity = INT16_MAX;
    outside_buff[sample].temperature = 0;
    outside_buff[sample].humidity = INT16_MAX;
  }

  TimerSet(&fridge_off_timer, 1);

  if (config->flags & CONFIG_FLAG_AUTOSTART) {
    ControllerEnable(true);
  }

  return rval;
}

void ControllerControl(th_value_t *values) {
  int32_t primary_t_avg = 0;
  int32_t outside_t_avg = 0;
  static bool enable_state = false;

  // Update value buffer with latest data
  primary_buff[buff_index].temperature =
      values[config->primary_sensor].temperature;
  primary_buff[buff_index].humidity = values[config->primary_sensor].humidity;
  outside_buff[buff_index].temperature =
      values[config->outside_sensor].temperature;
  outside_buff[buff_index].humidity = values[config->outside_sensor].humidity;

  buff_index = (buff_index + 1) & (CONTROLLER_BUFF_SAMPLES - 1);

  // Average temperatures
  for (uint16_t sample = 0; sample < CONTROLLER_BUFF_SAMPLES; sample++) {
    primary_t_avg += primary_buff[sample].temperature;
    outside_t_avg += outside_buff[sample].temperature;
  }

  primary_t_avg /= CONTROLLER_BUFF_SAMPLES;
  outside_t_avg /= CONTROLLER_BUFF_SAMPLES;

  if ((primary_t_avg > config->temp_set) &&
      (config->temp_set < outside_t_avg)) {
    if (TimerExpired(&fridge_off_timer)) {
      GPIO_SetBits(FRIDGE_PORT, (1 << FRIDGE_PIN));
      GPIO_SetBits(LED2_PORT, (1 << LED2_PIN));
      enable_state = true;
    }
  } else {
    GPIO_ResetBits(FRIDGE_PORT, (1 << FRIDGE_PIN));
    GPIO_ResetBits(LED2_PORT, (1 << LED2_PIN));

    // Only clear timer when changing states
    if (enable_state == true) {
      TimerSet(&fridge_off_timer, FRIDGE_OFF_TIME_M * 60 * 1000);
    }
    enable_state = false;
  }
}

void ControllerProcess() {
  int32_t rval;
  th_value_t values[CONFIG_MAX_SENSORS];

  if (!running) {
    return;
  }

  if (TimerExpired(&controller_timer)) {
    GPIO_SetBits(LED1_PORT, (1 << LED1_PIN));

    TimerSet(&controller_timer, config->period_ms);

    for (uint8_t sensor_id = 0; sensor_id < CONFIG_MAX_SENSORS; sensor_id++) {
      th_sensor_t *sensor = &config->sensor[sensor_id];
      if (sensor->addr != 0) {
        rval = Tca95xxaSetChannel(TCA95XXA_ADDR, sensor->bus);
        if (rval != 0) {
          dprint(ERR, "could not set i2c bus (%ld)\n", rval);
          GPIO_ResetBits(TCA_nRST_PORT, (1 << TCA_nRST_PIN));
          SleepMs(2);
          GPIO_SetBits(TCA_nRST_PORT, (1 << TCA_nRST_PIN));
          i2cSetup(100000);
          rval = Tca95xxaSetChannel(TCA95XXA_ADDR, sensor->bus);
          dprint(ERR, "Retry %d\n", rval);
          if (rval != 0) {
            break;
          }
          break;
        }

        rval = Sht31Read(sensor->addr, &values[sensor_id].temperature,
                          &values[sensor_id].humidity);
        if (rval != 0) {
          dprint(ERR, "SHT could not read temp/humidity for sensor%d (%ld)\n",
                 sensor_id, rval);
          i2cSetup(100000);  // Attempt to recover from I2C error
          break;
        }
      }
    }

    ControllerControl(values);

    dprint(DATA, "%s,", RtcGetTimeStr());

    for (uint8_t sensor_id = 0; sensor_id < CONFIG_MAX_SENSORS; sensor_id++) {
      th_sensor_t *sensor = &config->sensor[sensor_id];
      if (sensor->addr != 0) {
        int16_t temperature = values[sensor_id].temperature;
        int16_t humidity = values[sensor_id].humidity;
        char *sign = "";
        if (temperature < 0) {
          sign = "-";
          temperature *= -1;
        }
        dprint(OK_CONT, "%s%d.%02d,", sign, temperature / 100,
               (temperature - (temperature / 100) * 100));
        dprint(OK_CONT, "%d.%02d,", humidity / 100,
               (humidity - (humidity / 100) * 100));
      }
    }
    dprint(OK_CONT, "\n");

    GPIO_ResetBits(LED1_PORT, (1 << LED1_PIN));
  }
}

int32_t ControllerEnable(bool enabled) {
  if (enabled && !running) {
    config_t *config = ConfigGet();
    dprint(DATA, "timestamp,");
    for (uint8_t sensor_id = 0; sensor_id < CONFIG_MAX_SENSORS; sensor_id++) {
      th_sensor_t *sensor = &config->sensor[sensor_id];
      if (sensor->addr != 0) {
        dprint(OK_CONT, "sensor%d_t,sensor%d_h,", sensor_id, sensor_id);
      }
    }
    dprint(OK_CONT, "\n");

    TimerSet(&controller_timer, 1);
  } else if (!enabled) {
    TimerClear(&controller_timer);
  }

  running = enabled;

  return 0;
}
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

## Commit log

2016-09-29 Adding additional (analog) temperature sensors for inside/outside temp comparison
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2016-10-09 Start using the sqlite .execute() args to make sure the data is escaped for the query (just in case)
2016-10-09 Adding relay_status() to Ostur and exposing it via /relays on the control server
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2016-10-26 Silly way of changing filename case in OS X (Part 1)
2016-10-26 Silly way of changing filename case in OS X (Part 2)
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2016-11-10 Adding SHT breakout kicad files
    [sht31_breakout.kicad_pcb, sht31_breakout.sch]
2016-11-14 Start work on controller prototype
    [controller.kicad_pcb, controller.sch]
2016-11-15 Placement mostly done and half routed
    [controller.kicad_pcb, controller.sch]
2016-11-16 Passing DRC!
    [controller.kicad_pcb]
2016-11-16 Ostur Controller Layout 1.0 done!
    I think...
    [controller.kicad_pcb, controller.sch]
2016-11-28 Fixed GPIO label and moved resistor
    [controller.kicad_pcb]
2016-11-29 Updated part numbers for controller
    [controller.sch]
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2016-12-10 Start using board file and removing trailing spaces...
2016-12-10 Start adding I2C. Tx seems to be working
2016-12-10 Fixed i2c tx and rx now seems to be working too!
    [i2c.c, i2c.h]
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2017-01-04 Adding SHT console command
    NOTE: i2c is not stable yet. Stops working whenever a bad read happens.
    Need to debug...
2017-01-05 Add fix for i2c reads after NACK
    The transmit data register isn't cleared when a NACK occurs on
    the previous transaction. This manually flushes the register
    so the next one will work.
    [i2c.c]
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2017-01-06 Adding timer functions and using them on LED blink
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2017-01-06 Adding initial controller code (just prints values at interval)
2017-01-10 Adding simple relay board
    [relays.kicad_pcb, relays.sch]
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2017-01-12 Updated ostur controller to v1.1
    Some changes:
    Reduced i2c to 4 channels instead of 8
    Added ARM-SWD 10-pin connector
    Removed 8MHz crystal (not needed for usb)
    Added actual footprint for 32.768kHz crystal
    Moved uart, not sure why though...
    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
    [controller.kicad_pcb, controller.sch]
2017-01-18 Updating part numbers for ostur controller
    [controller.sch]
2017-01-18 Adding sheet details for ostur controller
    [controller.sch]
2017-01-18 Adding ostur controller BOM
    [controller-BOM.csv]
2017-01-18 Updating sht31 reset delay and address bug
    [sht31.c]
2017-01-18 Adding controller autoconfig command to auto-discover sht31 sensors
2017-01-18 Adding config fields for primary and outside sensors
2017-01-18 Update controller to sample all sensors, then print
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2017-01-18 Update sample rate to 2s and temp setting to 10C
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2017-01-21 Adding part numbers for relays board
    [relays-BOM.csv, relays.sch]
2017-01-25 Adding minimum off time for fridge
    To protect the compressor from short cycling
    [controller.c]
2017-01-26 Make sure SystemCoreClock() is correct even without 8MHz xtal
    [main.c]
2017-01-26 Update ostur.py so it doesn't time out so quick qaiting for sample
    [Ostur.py]
2017-01-27 Adding reset command
    For debugger-less remote restarts :D
    [console.c]
2017-01-27 Enable device RTC for real time and dates!
2017-01-27 Reverting to old timestamp until RTC drift is reduced
    [Ostur.py, controller.c]
2017-01-27 Try to recover from i2c errors in fw
    [controller.c]
2017-01-27 Don't crash when errors happen, just print them out...
    [Ostur.py]
2017-01-29 Fixed EE2-3NU Footprint
2017-01-29 Fix relay board after bad footprint fix
    [relays.kicad_pcb, relays.sch]
2017-01-31 Make tca driver more generic (for 4/8 ch parts)
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2017-02-02 Made much smaller SHT31 breakout
    We'll see if I can hand solder it...
    [sht31_breakout.kicad_pcb, sht31_breakout.sch]
2017-02-04 RTC crystal update for schematic and BOM
    [controller-BOM.csv, controller.sch]
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2017-02-04 Updating ostur controller!
    Removed unused headers
    Added extra shielding for 32768Hz crystal
    Made board smaller
    [controller-BOM.csv, controller.kicad_pcb, controller.sch]
2017-02-05 Cleaning up python drivers
    (Moving to silta repo)
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2017-02-12 Fixed silkscreen on parts
2017-02-19 Updating to newer kicad version
    [controller.sch]
2017-02-19 Adding labels for LSE in/out pins
    [controller.sch]
2017-03-11 Fixed controller PCB...
    Somehow I forgot to connect some VDD lines on the micocontroller.....
    [controller.kicad_pcb]
2017-03-11 something something kicad update....
    [controller.sch]
2017-03-11 Update pins for newest version
    [controller.sch]
2017-03-29 Fix merge screwup
    [controller-BOM.csv, controller.kicad_pcb, controller.sch]
2017-03-29 Fix i2c driver
2017-07-15 I2C Fix & #define Fix
    [i2c.c]
2017-07-15 Start designing flex pcb :D
    [sht31_breakout.kicad_pcb, sht31_breakout.sch]
2017-07-18 Added silkscreen and stiffener
    [sht31_breakout.kicad_pcb]
2017-08-19 Adding cheese wedges!
    [controller.kicad_pcb, controller.sch]
2017-08-19 Placement mostly done
    [controller.kicad_pcb, controller.sch]
2017-08-19 Layout done for Ostur Controller v1.3
    [controller.kicad_pcb, controller.sch]
2017-08-21 pyserial flush() is for output not input :( Fixed...
    [Ostur.py]
2017-08-21 Disabled echo and another usb not ready fix
    [uart.c]
2017-08-23 Catch Overflow errors during debug
    [ostur_log.py]
2017-09-09 Updating BOM for latest controller version
    [controller-BOM.csv]
2017-09-09 Add TCA95xx hard reset when unable to communicate
    [console.c, controller.c, sht31.c]
2017-09-10 Exit script on error for debugging
    Having signal integrity issues with Raspberry Pi near the fridge. The usb connection sometimes drops.
    Exiting the script for now. (I have a shell script that re-starts with alternating file descriptors for now)
    [ostur_log.py]
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2017-09-16 Adding DFU python script to get device in DFU mode and flash it!
    Example usage: dfu.py --filename controller/build/controller.bin --dev /dev/ttyACM0
2017-10-04 Updated sht31 breakout to be wedge shaped!
    [sht31_breakout.kicad_pcb, sht31_breakout.sch]
2017-10-04 Removed sensor breakouts from controller
    Updated silkscreen
    Removed SWD connector
    [controller.kicad_pcb, controller.sch]
2017-11-19 Fixed silkscreens on controller/sensor
    And submitted to pcbcart!
    [controller.kicad_pcb, sht31_breakout.kicad_pcb]
2017-11-26 Fix printing of negative floats
    [controller.c]
2017-11-26 Fix controller bugs
    Could only read from default sensor address, even when autodetecting the alternate.
    Added TCA95xx workaround for all cases
    [controller.c]
2018-01-22 Updated ostur_controller with NRF52810. Released v2.0
    [controller.kicad_pcb, controller.sch]
2018-02-02 Updating BOM and silkscreen fixes for controller 2.0
    [controller-BOM.csv, controller.kicad_pcb]
2018-02-04 First (semi-)working mynewt project
    For some reason it only works with a debugger attached :'(
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2018-02-04 Adding i2c, txa95xxa, and sht3x drivers
    I2C fails hard when a device NACK's though...
    [bsp.h, hal_bsp.c, main.c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]
2018-02-25 Minor fixes to work with latest mynewt-core
    [hal_bsp.c, syscfg.yml]
2018-03-03 Ostur FW 2.0 seems to be working!
    FW autodetects up to 8 SHT3x temp/humidity sensors and requires
    a minimum of 2 to run the fridge (one inside and one outside).
    Device beacons out each sensor temperature/humidity over BLE periodically
2018-07-20 Released Ostur Controller v2.1
    NOTE: Used kicad 5
    [controller.kicad_pcb, controller.sch]
2018-08-21 Adding db commit retries
    Having trouble while running with ostur_viewer in a raspberry pi
    zero
2019-06-29 Started working on ostur sensor
    [sensor.kicad_pcb, sensor.sch]
2019-07-02 Finished ostur sensor and released to oshpark
    [sensor.kicad_pcb, sensor.sch]
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2019-10-11 Released Ostur Sensor v1.1 to JLCPCB
    Changes:
    * Changed to 4 layer board for better RF performance
    * Changed RF trace to match 50Ohms on JLCPCB's JLC7628 stackup
    * Added decoupling capacitor for SHT3x
    * Changed I2C pull-ups to 0402's
    * Fixed silkscreen issues
    [sensor.kicad_pcb, sensor.sch]
2019-11-01 fixed de-duplication code
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2020-02-09 Stop using LFXO and start using LFRC
    Power consumption goes up from ~1uA idle to ~1.5-1.6uA
2020-07-10 sending mfg_data of size 1 is no longer allowed with latest NimBLE
    Changed to use magic value in packet instead of mfg data
    updated scanner to send up mfg data over serial
    updated ostur_logger to process both old and new packets
    [main.c, ostur_logger.py]
2020-07-10 fix possibly unaligned pointer code
    [main.c]
2021-01-02 Not sure why I never committed this.
    Using NRF52805
    [sensor.kicad_pcb, sensor.sch]
